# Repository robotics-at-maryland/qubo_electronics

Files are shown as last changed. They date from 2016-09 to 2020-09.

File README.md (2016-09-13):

# qubo_electronics

Welcome to the electronics repo for Project QUBO.
QUBO is an autonomous underwater vehicle and all of its electronics designs are stored here.

We use EAGLE for our circuit CAD.

eagleLibraries stores all the eagle libraries.

eagleDesigns sores all the boards that we design. Any design in this folder should ONLY USE COMPONENTS FROM THE eagleLibraries FOLDER.

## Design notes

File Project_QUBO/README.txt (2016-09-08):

This is the electronics folder for Project QUBO, the replacement for Tortuga 4.
===============================================================================

eagleLibraries is the EAGLE library folder.
	ALL robot PCB designs MUST only contain parts from libraries in the eagleLibraries directory.

datasheets is for all part datasheets used in the electronics designs.
	No subdirectories

eagleDesigns is for the actual eagle design files. 
	Subdirectories are created on a BOARD-BY-BOARD basis.
	If you're creating a new PCB, make a new folder. If you're editing an existing board, stay in the same folder.
	Use reason when creating new versions of files.

designDocumentation  is for design documentation.
	Use reason with file naming, no subdirectories.
	Document your design process ie. what your goal is, what options you considered, why you chose what you did, outline your final design selection, etc.
	Brownie points for LaTeX

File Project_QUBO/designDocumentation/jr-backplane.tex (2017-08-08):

\documentclass{article}

\usepackage{fancyhdr} % Required for custom headers
\usepackage{lastpage} % Required to determine the last page for the footer
\usepackage{extramarks} % Required for headers and footers
\usepackage[usenames,dvipsnames]{color} % Required for custom colors
\usepackage{graphicx} % Required to insert images
\usepackage{listings} % Required for insertion of code
\usepackage{courier} % Required for the courier font
\usepackage{amsfonts}
\usepackage{amsmath}
\usepackage{amssymb}
\usepackage{float}
\usepackage{siunitx}
\usepackage{hyperref}
\usepackage{wrapfig}

\graphicspath{ {Images/} }

%-------------------------------------------------------------------------------------------------
% DOCUMENT INFORMATION SPECIFIED HERE
%-------------------------------------------------------------------------------------------------
%% Assignment type, e.g. HW1, Project 2, Assignment 3
\newcommand{\assignmentType}{Interface Control Document}

%% Assignment title, e.g. Karger's Min Cut, Magnetic Fields
\newcommand{\assignmentTitle}{Qubo Electrical System}

%% Course number, e.g. ENEE324
\newcommand{\courseNum}{RoboSub 2017}

%% Course title, e.g. Advanced Signals and Systems
\newcommand{\courseTitle}{Submarine Hackathon}

%% Course professor
\newcommand{\prof}{RoboNation}

%% Department
\newcommand{\dept}{Department of Electrical and Computer Engineering}						

%% University
\newcommand{\univ}{University of Maryland}	

%% Seal image
\newcommand{\seal}{UMD_seal.png}					

%% Author
\newcommand{\student}{Ben Hurwitz}

% Margins
\topmargin=-0.45in
\evensidemargin=0in
\oddsidemargin=0in
\textwidth=6.5in
\textheight=9.0in
\headsep=0.25in

\linespread{0.9} % Line spacing

% Set up the header and footer
\pagestyle{fancy}
\rhead{\student} % Top left header
\lhead{\courseTitle : \assignmentType} % Top center head
%\rhead{\firstxmark} % Top right header
\lfoot{Last built:\ \today} % Bottom left footer
\cfoot{} % Bottom center footer
\rfoot{Page\ \thepage\ of\ \protect\pageref{LastPage}} % Bottom right footer
\renewcommand\headrulewidth{0.4pt} % Size of the header rule
\renewcommand\footrulewidth{0.4pt} % Size of the footer rule

\setlength\parindent{0pt} % Removes all indentation from paragraphs

\begin{document}

%----------------------------------------------------------------------------------------
%	TITLE PAGE
%----------------------------------------------------------------------------------------

\begin{titlepage}
    \begin{center}
        \vspace*{1cm}
        
        \Huge
        \textbf{\assignmentTitle}
        
        \vspace{0.5cm}
        \LARGE
        \assignmentType
        
        \vspace{1.5cm}
        
        \textbf{\student}
        
        \vfill
        
        \vspace{0.6cm}
        
        
        
        \vfill
        
        \Large
        \today	\\
        \courseNum : \courseTitle \\
        \prof \\
        \dept \\
        \univ \\
        
    \end{center}
\end{titlepage}

\tableofcontents
\listoffigures
\listoftables

\pagebreak

\section{Overview}
RoboSub 2017 came in a hurry, with little electrical working properly. The charging system lacked testing, the ORing chips had not demonstrated full capabilities, and the LT8640 5V/12V rail generators were completely unresponsive. This is to say that there was justification for the decision to scrap the charging and the LT8640s entirely for the far more reliable (and better known) PTN78020, the wide-range input 6A DC/DC buck converter made by TI that is controlled by a single resistor. It was a changed intended to make things simpler and improve robustness with known quantities. Instead, it pushed us (and by us, I mean me) towards to panic-region. In keeping with the Robotics At Maryland (RAM, or R@M) spirit, when we got to competition, none of the boards that were developed worked in any meaningful way, and thus we were forced to decide: spend time debugging, which was not something we are good at, or spend time further simplifying and hack it to get exactly the minimum of what was needed. By the end of day two, we had opted for the latter.
\paragraph{}
The resulting system was close to as barebones as could be, and by the time we actually went in and completed our qualifying run, the system was, in my opinion, the most minimalist system possible for our configuration. We had removed nearly all the sensors entirely, including the AHRS, depth, and internal temperature, choosing to rely simply on our mechanical stability and dead-reckoning to get us through. Thermal considerations were lost, or left to passive cooling options. The power control modules for the batteries were jettisoned for simple SPST switches and 30A fuses. Even the PCA9685 chips that we were using for PWM signalling were tossed aside. But in it's simplicity, Qubo worked for the first time, and qualification was achieved, so in this there was success where there had not been before. The system cuts out all the fat from previous iterations and reduces the entire electrical subsystem to a half dozen major components, including all voltage generation, that allowed Qubo to move forward.

\section{Details}
I have no images to show you at all, so if you'd like a more hands on view of the system, we should facetime or skype or whatever you kids use these days to go through it. The system runs off of a single battery, which was triggered by a simple SPST rocker switch to avoid the issues associated with plugging live power into other components. This 14.8V nominal goes through a single PTN, which is resistor-set (2.61kO) to output about 10V. (Why 10V? Because the PTN needs a 3V cushion to do it's converting, and a 12V output would require a minimum of 15V, not really feasible with this.) This 10V powers the Jetson (which takes down to 7V), and through the magnetic reed switch, triggers the main thruster relay. There are a number of capacitors on the input to the PTN - \textbf{DO NOT REMOVE THESE!!} Each of the ESCs on the output of the relay has a 220uF capacitor on it, which draws a large inrush current when voltage is applied. This causes significant voltage drop down to nearly 5V of the input source (batteries or shore), which kills the PTN, and thus kills the Jetson. The extra caps at the input of the PTN (notice how close they are) prevent this droop from being seen by the PTN, thus keeping it in operation. The ESCs themselves are mostly the same, except for the PWM signal generator. The PCA chip shorted, and we didn't have a backup, so we switched the embedded Arduino Uno to a TeensyDuino (TD), which has a dozen or so PWM outputs built-in. The TD is connected to the Jetson via a USB cable, which also power it. This gives us the ability to easily generate PWM signals directly from the embedded system. The only other thing is a single NCP1117 that converts the battery/shore voltage into 5V for the ethernet switch.
\paragraph{}
That, in essence, is the entire system. A single 10V rail powers the Jetson, which powers the embedded, and switches the thrusters on and off. Viola.

\section{Extras}
There are so many wires and so many parts that are still there but left unused or unconnected that it's hard to see this simplicity. The terminal block is used mostly to connect all the ESCs to the same high-voltage (V\_Batt) input, and to connect their outputs to the same ground. A second NCP1117 is left hanging and disconnected; it was used for some other bits that got summarily culled from the robot. There is a depth sensor which we believe (\textbf{but are not sure}) shorted at some point, thus rendering its data worthless. The AHRS works, but it's not reliable with all the changing currents within the pressure vessel. There are loose wires from two fans that were initially part of the vehicle as well - they are 3-wire black ribbon cables. The I2C line was removed entirely because of the removal of all associated devices, but the wires still remain. All the PWMs from the ESCs are bundled together into the TD; the signal and power grounds are tied together for simplicity; and the power and ground lines go right into the terminal block. 

\section{Moving Forward}
To be frank, the system looks like shit. It needs a good cleaning up. But I cannot emphasize enough that \textbf{it works}. Do not take this for granted! It is not easy to get all of this working, and tearing it down to make it look pretty will put a lot of pressure on you to build it back up again. It was tricky enough once. Use it as a platform to continue forward with, to build off of. Personally, I would use this next year to design small boards for each of the primary components (5V generator (PTN), 10V generator (PTN), TD), thoroughly test these, then combine them into a larger board with the necessary inputs and outputs. I would spend the first semester doing this; they're also smaller projects that can be given to new students without too much risk since they're all only a half dozen small components each at most. Make sure that the ESCs can more easily attach to the board! It should be a decent project for you. Pay close attention to how the wiring will be laid out! A major disappointment was not taking the wiring into enough consideration. It's a major size, weight, and obnoxious consideration. Take some time to think about how the wires should lay out, and discuss with Peter. Try to pull together mock-ups if you can, it'll help to visualize where things should be. 
\paragraph{}
If you get a nice single board that houses the single input, the 5V/10V generators, and the TD, and it has been tested thoroughly, then there are a number of small additional projects that can be developed. Add back in the depth sensor first. A single 5V I2C line \textbf{should} suffice, even though the Bar30 asks for a 3.3V I2C line (this has been bourne out in other testing, but you should verify! Collaborate with the software team on building a small jig to test this). The AHRS connects directly to the Jetson, so this is not a concern of yours, but something to keep in mind is shielding it from stray magnetic fields - use your PHYS271 and ENEE380/1 knowledge for this! (Moving charges generate magnetic fields.) Add some internal sensors - I'm thinking temperature in particular - using the same method: build a small component-specific board, test it completely, then integrate it into the larger board. Current and voltage sensors would also be nice, but those are something that a new EE can do without being critical to the system. 
\paragraph{}
My sense is that the critical parts on a single board can take a semester. For the second semester, focus on less critical, perhaps more long terms components. For this, you might consider integrating the DVL. We have the UWE isolated regulator already, and you can work through the noise reduction stuff while the other EEs develop the current sensor + fuse circuit we had previously for each of the thruster outputs. By next year's competition, you should be shooting for a very robust power system that is essentially a cleaner version of what I hacked together. Do not wait! Starting too late was a huge failure on my part. Get boards out to fab within a few weeks of starting, and continuously iterate. Note that for small boards, OshPark is fantastic (takes a bit longer, but only \$5 a square inch), while larger boards can be made with Advanced Circuit's \$33 deal. New EEs are developing breakout board for certain components. BUT the best thing you can do to make everyone's lives easier is to learn to use Design Blocks in Eagle. These will allow you to easily move a design from a smaller board to a larger one without any extra work. 
\paragraph{}
I won't tell you what to do, only suggest. But I believe it would be a colossal mistake to throw away the system as it is now to redesign again. Use what you have to test, and develop slowly. You have a nice foundation; don't throw it away because it looks like crap.
\par
Slack me if you have questions and I can try to help. Good luck with it - think of it as a bundle of small parts, and it becomes very doable.

\end{document}

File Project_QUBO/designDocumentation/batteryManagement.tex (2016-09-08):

\documentclass[12pt, letterpaper]{article}

\usepackage{amsmath}
\usepackage[margin=1in]{geometry}

\begin{document}
	\section{Design Goals}
		At a system level, the battery management subsystem lies between the batteries and the power supply/regulation system. The battery management system is responsible for balancing the batteries to create a single high voltage bus capable of powering all of the robot subsystems. It manages multiple battery cells (6 cells in Tortuga 4, 2 cells in Project QUBO). It must be capable of dealing with batteries of differing charge levels and therefore different voltages. Each battery is not capable of powering the entire robot so load balancing between the batteries, even with batteries of different voltages, is required. The battery management system is also responsible for providing a system to monitor the batteries and their containers. These monitoring systems include hot-plug detection, water sensors, and temperature sensors. Since Project QUBO contains two separate battery packs, hot-swapping support in the battery management system would also be desirable.
		
		\paragraph{General Goals}
		\begin{itemize}
			\item Balance 2 batteries and present a single battery-level rail to draw power from
			\item Provide a monitoring interface to ensure safe performance of the batteries
			\item Provide a method for connecting shore power to the robot
			\item Provide a method for turning battery power on/off
			\item Evaluate and possibly integrate hot-swapping functionality
		\end{itemize}
		
	\section{System Layout}
		
		Currently (March 2015), each of the 2 batteries will reside in their own hulls that are separate from the main electronics hull. This allows for easy battery removal from the system and for a smaller, simpler electronics hull. The battery management system is split between the electronics hull and battery hulls. Moreover, some of the battery management circuitry will reside on the same backplane PCB as the power regulation/distribution board. While this makes the power system more monolithic in nature, it will make systems integration on the robot much simpler since there will be only one power supply related board on the backplane.
		
		The battery management system will consist of two PCBs. One PCB will contain the balancing and hot-swapping circuitry and will be plugged into the backplane inside the main electronics hull. That PCB will be shared with the power regulation/distribution system. The other PCB will reside inside the battery hulls (so technically there will be 3 PCBs in the system since there are 2 battery hulls). The battery hull PCB will contain a mechanism to turn a battery on/off and provide monitoring circuitry to ensure the battery is functioning properly/safely inside the battery hulls.
		
	\section{Battery Balancing}
	
		In designing the battery balancing portion of the system, we found 2 possible methods for balancing the batteries to generate a single bus for the robot. We evaluated each method by taking efficiency, cost, and simplicity into account. 
		
		The first method is diode-ORing. This is the same method used the balance the 6 batteries (the main battery contained 5 27V batteries and the 6th 'cell' was the shore power) inside of Tortuga 4. 
\end{document}

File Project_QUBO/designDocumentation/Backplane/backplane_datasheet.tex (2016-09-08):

\documentclass{article}

\usepackage{fancyhdr} % Required for custom headers
\usepackage{lastpage} % Required to determine the last page for the footer
\usepackage{extramarks} % Required for headers and footers
\usepackage[usenames,dvipsnames]{color} % Required for custom colors
\usepackage{graphicx} % Required to insert images
\usepackage{listings} % Required for insertion of code
\usepackage{courier} % Required for the courier font
\usepackage{amsfonts}
\usepackage{amsmath}
\usepackage{amssymb}

%-------------------------------------------------------------------------------------------------
% DOCUMENT INFORMATION SPECIFIED HERE
%-------------------------------------------------------------------------------------------------
%% Assignment type, e.g. HW1, Project 2, Assignment 3
\newcommand{\assignmentType}{Technical Datasheet}

%% Assignment title, e.g. Karger's Min Cut, Magnetic Fields
\newcommand{\assignmentTitle}{Backplane}

%% Last edited date
\newcommand{\lastEdited}{8/2/16}

%% Course number, e.g. ENEE324
\newcommand{\courseNum}{}

%% Course title, e.g. Advanced Signals and Systems
\newcommand{\courseTitle}{Robotics@Maryland}

%% Course professor
\newcommand{\prof}{Institute for Systems Research}

%% Department
\newcommand{\dept}{Department of Electrical and Computer Engineering}						

%% University
\newcommand{\univ}{University of Maryland}	

%% Seal image
\newcommand{\seal}{C:/UMD_seal.png}					

%% Author
\newcommand{\student}{Ben Hurwitz}

% Margins
\topmargin=-0.45in
\evensidemargin=0in
\oddsidemargin=0in
\textwidth=6.5in
\textheight=9.0in
\headsep=0.25in

\linespread{0.9} % Line spacing

% Set up the header and footer
\pagestyle{fancy}
\rhead{\author} % Top left header
\lhead{\courseTitle : \assignmentType} % Top center head
%\rhead{\firstxmark} % Top right header
\lfoot{\lastxmark} % Bottom left footer
\cfoot{} % Bottom center footer
\rfoot{Page\ \thepage\ of\ \protect\pageref{LastPage}} % Bottom right footer
\renewcommand\headrulewidth{0.4pt} % Size of the header rule
\renewcommand\footrulewidth{0.4pt} % Size of the footer rule

\setlength\parindent{0pt} % Removes all indentation from paragraphs

\begin{document}

%----------------------------------------------------------------------------------------
%	TITLE PAGE
%----------------------------------------------------------------------------------------

\begin{titlepage}
    \begin{center}
        \vspace*{1cm}
        
        \Huge
        \textbf{\assignmentTitle}
        
        \vspace{0.5cm}
        \LARGE
        \assignmentType
        
        \vspace{1.5cm}
        
        \textbf{\student}
        
        \vfill
        
        \vspace{0.6cm}
        
        
        
        \vspace{1.5cm}
        
        \textbf{Last Edited: \lastEdited}
        
        \vfill
        
        \Large
        \courseTitle \\
        \prof \\
        \dept \\
        \univ \\
        
    \end{center}
\end{titlepage}

\tableofcontents

\section{Introduction}
The backplane is a four layer board that connects most of the electrical components together and passes signals between them. Physically, the board is approximately 20cm long and 10cm wide, sitting about 3.5 inches above the bottom of the electronics hulls, and consists of a 16V plane, a GND plane, and two internal signal planes. There are four major connectors for the fours plug-in daughterboards, which allow for flexibility and modularity, each with eighty signal pins and two full-power blades. There are two I$^2$C lines, two SPI lines, and two serial RX/TX lines that run between the CPU and all the daughterboards, as well as USB connections between the CPU and the individual daughterboards. 

\section{Connectors}
\subsection{Daughterboard Connection}
\subsection{CPU Connection}
\subsection{Hypertronics Connection}

\section{Signalling}
\subsection{USB}
\subsection{I$^2$C}
\subsection{SPI}
\subsection{Serial}

\section{Thrusters}

\section{Misc}
\subsection{Current Sensors}
\subsection{Debug port}
\subsection{Misc. Ports}

\section{Appendix}
\subsection{Current ratings}
\subsection{Thermal Considerations}
\subsection{Complete Parts List}

\end{document}

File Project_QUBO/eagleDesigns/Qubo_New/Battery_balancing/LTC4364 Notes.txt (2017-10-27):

LTC4364 Notes
	-M1 is normally fully on
	-When there is an overvoltage, the voltage amplifier controls the M1 gate and regulates
	 the voltage at the OUT pin set by the external resistive divider to ground and the internal 1.25 V reference
	-Overcurrent can be detected by the current sensing resistor between the SENSE and OUT pins
	-An IA (active current limit circuit) controls the gate of M1 to limit the sense voltage to 50mV if OUT is above 2.5V
	-During OV or OI event, a current source starts charging the TMR cap.  The pull-up current source in an OI event is 5 
	 times that of one in an OC event.  When TMR reaches 1.25V, FLT pulls low to warn impending turn off.  M1 stays on until
	 TMR reaches 1.35V, at which point HGATE pulls low and turns off M1. 
	-Fault timer period decreases with voltage across the MOSFET
	-If HGATE is latched low, briefly pulling SHDN below 0.5V resets the fault and lets HGATE pull high
	-The source and drain of MOSFET M2 act as the anode and cathode of the ideal diode
	-DGATE maintains a 30mV voltage across source and drain of M2.
	-If a reverse voltage exceeding -30mV flows across M2, DGATE pulls low and turns off M2
	-If VCC falls below GND voltage, DGATE is pulled to SOURCE pin voltage, keeping M2 off.  
	-If HGATE pulls low, DGATE also pulls low
	-If the output drops below GND, HGATE is pulled to SOURCE pin voltage, turning M1 off and shutting down the forward current
	 path
	-If UV detects an undervoltage, HGATE and DGATE remain low if UV is below its 1.25V threshold.  SHDN turns off both the
	 pass devices and internal circuitry, reducing supply current to 10uA.

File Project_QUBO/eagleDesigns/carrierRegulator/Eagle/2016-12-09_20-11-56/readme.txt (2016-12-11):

 

**********************************************************
*************  Important Instructions Follow  ************
**********************************************************
 
All files exported to: Z:\\48\\23\\4823925\\8\Eagle\2016-12-09_20-11-56\2016-12-09_20-11-56.xml

To import your new library into Eagle:
1. Start Eagle.
2. Select File -> New -> Library from the menu.
3. In the blank library window, select File -> Execute Script from the menu.
5. Browse to your newly exported Eagle Script file (".scr" file extension)
6. After opening the file, the script will populate the new library.
7. Use File -> Save (or Save As..) to save the library to the desired location in Eagle native format.

For additional information, please visit this site:
http://www.accelerated-designs.com/help/Eagle_import.html

You may also find this video helpful:
http://youtu.be/5jGuWY-Yy3Q

Component "GRM216R71H103KA01D" renamed to "GRM216R71H103KA01D"
Component "CC0805KRX7R9BB682" renamed to "CC0805KRX7R9BB682"
Component "CL21C271JBANFNC" renamed to "CL21C271JBANFNC"
Component "WB_CURRENT_LOAD" renamed to "WB_CURRENT_LOAD"
Component "C0805C104K5RACTU" renamed to "C0805C104K5RACTU"
Component "16SVPE180M" renamed to "16SVPE180M"
Component "CC0805KRX7R9BB681" renamed to "CC0805KRX7R9BB681"
Component "EMK212B7105KG-T" renamed to "EMK212B7105KG-T"
Component "B230A-13-F" renamed to "B230A-13-F"
Component "WB_GND" renamed to "WB_GND"
Component "PM2110-5R6M-RC" renamed to "PM2110-5R6M-RC"
Component "CSD17310Q5A" renamed to "CSD17310Q5A"
Component "CSD18537NQ5A" renamed to "CSD18537NQ5A"
Component "ERJ-6ENF8061V" renamed to "ERJ-6ENF8061V"
Component "ERJ-6ENF1004V" renamed to "ERJ-6ENF1004V"
Component "ERJ-6ENF1101V" renamed to "ERJ-6ENF1101V"
Component "ERJ-6ENF9761V" renamed to "ERJ-6ENF9761V"
Component "ERJ-6ENF4753V" renamed to "ERJ-6ENF4753V"
Component "CSNL1206FT3L00" renamed to "CSNL1206FT3L00"
Component "ERJ-6ENF1272V" renamed to "ERJ-6ENF1272V"
Component "ERJ-6ENF3161V" renamed to "ERJ-6ENF3161V"
Component "ERJ-6ENF2612V" renamed to "ERJ-6ENF2612V"
Component "LM25116MHX/NOPB" renamed to "LM25116MHX/NOPB"
Component "WB_BATTERY" renamed to "WB_BATTERY"
Component "GRM31CR71H475KA12L" renamed to "GRM31CR71H475KA12L"
The Symbol WB_CONTINUATION was missing a RefDes attribute, a refdes was created for the symbol.
The Symbol WB_CONTINUATION was missing a Type attribute, a type was created for the symbol.
The Symbol WB_CONTINUATION was missing a Value attribute, a value was created for the symbol.
The Symbol WB_CAP_OUTPUT was missing a RefDes attribute, a refdes was created for the symbol.
The Symbol WB_CAP_OUTPUT was missing a Type attribute, a type was created for the symbol.
The Symbol WB_CAP_OUTPUT was missing a Value attribute, a value was created for the symbol.
The Symbol WB_DIODE was missing a RefDes attribute, a refdes was created for the symbol.
The Symbol WB_DIODE was missing a Type attribute, a type was created for the symbol.
The Symbol WB_DIODE was missing a Value attribute, a value was created for the symbol.
The Symbol WB_CURRENT_PROBE was missing a RefDes attribute, a refdes was created for the symbol.
The Symbol WB_CURRENT_PROBE was missing a Type attribute, a type was created for the symbol.
The Symbol WB_CURRENT_PROBE was missing a Value attribute, a value was created for the symbol.
The Symbol WB_N_MOSFET was missing a RefDes attribute, a refdes was created for the symbol.
The Symbol WB_N_MOSFET was missing a Type attribute, a type was created for the symbol.
The Symbol WB_N_MOSFET was missing a Value attribute, a value was created for the symbol.
The Symbol WB_BLOCK_IO was missing a RefDes attribute, a refdes was created for the symbol.
The Symbol WB_BLOCK_IO was missing a Type attribute, a type was created for the symbol.
The Symbol WB_BLOCK_IO was missing a Value attribute, a value was created for the symbol.
The Symbol WB_LM25116 was missing a RefDes attribute, a refdes was created for the symbol.
The Symbol WB_LM25116 was missing a Type attribute, a type was created for the symbol.
The Symbol WB_LM25116 was missing a Value attribute, a value was created for the symbol.
The Symbol WB_VOLTAGE_PROBE was missing a RefDes attribute, a refdes was created for the symbol.
The Symbol WB_VOLTAGE_PROBE was missing a Type attribute, a type was created for the symbol.
The Symbol WB_VOLTAGE_PROBE was missing a Value attribute, a value was created for the symbol.
The Symbol WB_PWL_CURRENT_LOAD was missing a RefDes attribute, a refdes was created for the symbol.
The Symbol WB_PWL_CURRENT_LOAD was missing a Type attribute, a type was created for the symbol.
The Symbol WB_PWL_CURRENT_LOAD was missing a Value attribute, a value was created for the symbol.
The Symbol WB_PWL_VOLTAGE_SOURCE was missing a RefDes attribute, a refdes was created for the symbol.
The Symbol WB_PWL_VOLTAGE_SOURCE was missing a Type attribute, a type was created for the symbol.
The Symbol WB_PWL_VOLTAGE_SOURCE was missing a Value attribute, a value was created for the symbol.
The Symbol WB_SOURCE_RESISTOR was missing a RefDes attribute, a refdes was created for the symbol.
The Symbol WB_SOURCE_RESISTOR was missing a Type attribute, a type was created for the symbol.
The Symbol WB_SOURCE_RESISTOR was missing a Value attribute, a value was created for the symbol.
The Symbol WB_PRIM_PWL_VOLTAGE_SOURCE was missing a RefDes attribute, a refdes was created for the symbol.
The Symbol WB_PRIM_PWL_VOLTAGE_SOURCE was missing a Type attribute, a type was created for the symbol.
The Symbol WB_PRIM_PWL_VOLTAGE_SOURCE was missing a Value attribute, a value was created for the symbol.
The Symbol WB_PRIMITIVE_BATTERY was missing a RefDes attribute, a refdes was created for the symbol.
The Symbol WB_PRIMITIVE_BATTERY was missing a Type attribute, a type was created for the symbol.
The Symbol WB_PRIMITIVE_BATTERY was missing a Value attribute, a value was created for the symbol.
The Symbol WB_PRIM_AC_VOLTAGE_SOURCE was missing a RefDes attribute, a refdes was created for the symbol.
The Symbol WB_PRIM_AC_VOLTAGE_SOURCE was missing a Type attribute, a type was created for the symbol.
The Symbol WB_PRIM_AC_VOLTAGE_SOURCE was missing a Value attribute, a value was created for the symbol.
The Symbol WB_SYNC_CAPACITOR was missing a RefDes attribute, a refdes was created for the symbol.
The Symbol WB_SYNC_CAPACITOR was missing a Type attribute, a type was created for the symbol.
The Symbol WB_SYNC_CAPACITOR was missing a Value attribute, a value was created for the symbol.
The Symbol WB_PRIMITIVE_INDUCTOR was missing a RefDes attribute, a refdes was created for the symbol.
The Symbol WB_PRIMITIVE_INDUCTOR was missing a Type attribute, a type was created for the symbol.
The Symbol WB_PRIMITIVE_INDUCTOR was missing a Value attribute, a value was created for the symbol.
The Symbol WB_PRIM_STARTUP_VOLTAGE_SOURCE was missing a RefDes attribute, a refdes was created for the symbol.
The Symbol WB_PRIM_STARTUP_VOLTAGE_SOURCE was missing a Type attribute, a type was created for the symbol.
The Symbol WB_PRIM_STARTUP_VOLTAGE_SOURCE was missing a Value attribute, a value was created for the symbol.
The Symbol WB_STARTUP_VOLTAGE_SOURCE was missing a RefDes attribute, a refdes was created for the symbol.
The Symbol WB_STARTUP_VOLTAGE_SOURCE was missing a Type attribute, a type was created for the symbol.
The Symbol WB_STARTUP_VOLTAGE_SOURCE was missing a Value attribute, a value was created for the symbol.
The Symbol WB_LOAD_RESISTOR was missing a RefDes attribute, a refdes was created for the symbol.
The Symbol WB_LOAD_RESISTOR was missing a Type attribute, a type was created for the symbol.
The Symbol WB_LOAD_RESISTOR was missing a Value attribute, a value was created for the symbol.

Ultra Librarian Gold 8.1.204 Process Report

Message - Padstack "RX44Y57D0T" Shape(4) is a CIRCLE with no diameter.
Message - Padstack "RX44Y71D0T" Shape(4) is a CIRCLE with no diameter.
Message - Padstack "RX128Y32D0T" Shape(4) is a CIRCLE with no diameter.
Message - Padstack "RX86Y64D0T" Shape(4) is a CIRCLE with no diameter.
Message - Padstack "RX200Y700D0T" Shape(4) is a CIRCLE with no diameter.
Message - Padstack "RX31p5Y27p56D0T" Shape(4) is a CIRCLE with no diameter.
Message - Padstack "RX4p3Y4p56D0T" Shape(4) is a CIRCLE with no diameter.
Message - Padstack "RX56Y14D0T" Shape(4) is a CIRCLE with no diameter.
Message - Padstack "RX124Y171D0T" Shape(4) is a CIRCLE with no diameter.
Message - Component "GRM216R71H103KA01D" attribute "Cap" references text style "" that is not in the database.
The default pattern text style "H50s3" was substituted.
Message - Component "GRM216R71H103KA01D" attribute "ESR" references text style "" that is not in the database.
The default pattern text style "H50s3" was substituted.
Message - Component "GRM216R71H103KA01D" attribute "IRMS" references text style "" that is not in the database.
The default pattern text style "H50s3" was substituted.
Message - Component "GRM216R71H103KA01D" attribute "VDC" references text style "" that is not in the database.
The default pattern text style "H50s3" was substituted.
Message - Component "CC0805KRX7R9BB682" attribute "Cap" references text style "" that is not in the database.
The default pattern text style "H50s3" was substituted.
Message - Component "CC0805KRX7R9BB682" attribute "ESR" references text style "" that is not in the database.
The default pattern text style "H50s3" was substituted.
Message - Component "CC0805KRX7R9BB682" attribute "IRMS" references text style "" that is not in the database.
The default pattern text style "H50s3" was substituted.
Message - Component "CC0805KRX7R9BB682" attribute "VDC" references text style "" that is not in the database.
The default pattern text style "H50s3" was substituted.
Message - Component "CL21C271JBANFNC" attribute "Datasheet URL" references text style "" that is not in the database.
The default pattern text style "H50s3" was substituted.
Message - Component "CL21C271JBANFNC" attribute "Cap" references text style "" that is not in the database.
The default pattern text style "H50s3" was substituted.
Message - Component "CL21C271JBANFNC" attribute "ESR" references text style "" that is not in the database.
The default pattern text style "H50s3" was substituted.
Message - Component "CL21C271JBANFNC" attribute "IRMS" references text style "" that is not in the database.
The default pattern text style "H50s3" was substituted.
Message - Component "CL21C271JBANFNC" attribute "VDC" references text style "" that is not in the database.
The default pattern text style "H50s3" was substituted.
Message - Component "C0805C104K5RACTU" attribute "Cap" references text style "" that is not in the database.
The default pattern text style "H50s3" was substituted.
Message - Component "C0805C104K5RACTU" attribute "ESR" references text style "" that is not in the database.
The default pattern text style "H50s3" was substituted.
Message - Component "C0805C104K5RACTU" attribute "IRMS" references text style "" that is not in the database.
The default pattern text style "H50s3" was substituted.
Message - Component "C0805C104K5RACTU" attribute "VDC" references text style "" that is not in the database.
The default pattern text style "H50s3" was substituted.
Message - Component "16SVPE180M" attribute "Datasheet URL" references text style "" that is not in the database.
The default pattern text style "H50s3" was substituted.
Message - Component "16SVPE180M" attribute "Cap" references text style "" that is not in the database.
The default pattern text style "H50s3" was substituted.
Message - Component "16SVPE180M" attribute "ESR" references text style "" that is not in the database.
The default pattern text style "H50s3" was substituted.
Message - Component "16SVPE180M" attribute "IRMS" references text style "" that is not in the database.
The default pattern text style "H50s3" was substituted.
Message - Component "16SVPE180M" attribute "VDC" references text style "" that is not in the database.
The default pattern text style "H50s3" was substituted.
Message - Component "CC0805KRX7R9BB681" attribute "Cap" references text style "" that is not in the database.
The default pattern text style "H50s3" was substituted.
Message - Component "CC0805KRX7R9BB681" attribute "ESR" references text style "" that is not in the database.
The default pattern text style "H50s3" was substituted.
Message - Component "CC0805KRX7R9BB681" attribute "IRMS" references text style "" that is not in the database.
The default pattern text style "H50s3" was substituted.
Message - Component "CC0805KRX7R9BB681" attribute "VDC" references text style "" that is not in the database.
The default pattern text style "H50s3" was substituted.
Message - Component "EMK212B7105KG-T" attribute "Cap" references text style "" that is not in the database.
The default pattern text style "H50s3" was substituted.
Message - Component "EMK212B7105KG-T" attribute "ESR" references text style "" that is not in the database.
The default pattern text style "H50s3" was substituted.
Message - Component "EMK212B7105KG-T" attribute "IRMS" references text style "" that is not in the database.
The default pattern text style "H50s3" was substituted.
Message - Component "EMK212B7105KG-T" attribute "VDC" references text style "" that is not in the database.
The default pattern text style "H50s3" was substituted.
Message - Component "B230A-13-F" attribute "Datasheet URL" references text style "" that is not in the database.
The default pattern text style "H50s3" was substituted.
Message - Component "B230A-13-F" attribute "Io" references text style "" that is not in the database.
The default pattern text style "H50s3" was substituted.
Message - Component "B230A-13-F" attribute "VRRM" references text style "" that is not in the database.
The default pattern text style "H50s3" was substituted.
Message - Component "B230A-13-F" attribute "VFatIo" references text style "" that is not in the database.
The default pattern text style "H50s3" was substituted.
Message - Component "PM2110-5R6M-RC" attribute "L" references text style "" that is not in the database.
The default pattern text style "H50s3" was substituted.
Message - Component "PM2110-5R6M-RC" attribute "DCR" references text style "" that is not in the database.
The default pattern text style "H50s3" was substituted.
Message - Component "PM2110-5R6M-RC" attribute "IDC" references text style "" that is not in the database.
The default pattern text style "H50s3" was substituted.
Message - Component "CSD17310Q5A" attribute "Datasheet URL" references text style "" that is not in the database.
The default pattern text style "H50s3" was substituted.
Message - Component "CSD17310Q5A" attribute "VdsMax" references text style "" that is not in the database.
The default pattern text style "H50s3" was substituted.
Message - Component "CSD17310Q5A" attribute "IdsMax" references text style "" that is not in the database.
The default pattern text style "H50s3" was substituted.
Message - Component "CSD17310Q5A" attribute "Rdson45" references text style "" that is not in the database.
The default pattern text style "H50s3" was substituted.
Message - Component "CSD17310Q5A" attribute "QgTyp" references text style "" that is not in the database.
The default pattern text style "H50s3" was substituted.
Message - Component "CSD17310Q5A" attribute "Quantity" references text style "" that is not in the database.
The default pattern text style "H50s3" was substituted.
Message - Component "ERJ-6ENF8061V" attribute "Resistance" references text style "" that is not in the database.
The default pattern text style "H50s3" was substituted.
Message - Component "ERJ-6ENF8061V" attribute "Power" references text style "" that is not in the database.
The default pattern text style "H50s3" was substituted.
Message - Component "ERJ-6ENF8061V" attribute "Tolerance" references text style "" that is not in the database.
The default pattern text style "H50s3" was substituted.
Message - Component "ERJ-6ENF1004V" attribute "Resistance" references text style "" that is not in the database.
The default pattern text style "H50s3" was substituted.
Message - Component "ERJ-6ENF1004V" attribute "Power" references text style "" that is not in the database.
The default pattern text style "H50s3" was substituted.
Message - Component "ERJ-6ENF1004V" attribute "Tolerance" references text style "" that is not in the database.
The default pattern text style "H50s3" was substituted.
Message - Component "ERJ-6ENF1101V" attribute "Resistance" references text style "" that is not in the database.
The default pattern text style "H50s3" was substituted.
Message - Component "ERJ-6ENF1101V" attribute "Power" references text style "" that is not in the database.
The default pattern text style "H50s3" was substituted.
Message - Component "ERJ-6ENF1101V" attribute "Tolerance" references text style "" that is not in the database.
The default pattern text style "H50s3" was substituted.
Message - Component "ERJ-6ENF9761V" attribute "Resistance" references text style "" that is not in the database.
The default pattern text style "H50s3" was substituted.
Message - Component "ERJ-6ENF9761V" attribute "Power" references text style "" that is not in the database.
The default pattern text style "H50s3" was substituted.
Message - Component "ERJ-6ENF9761V" attribute "Tolerance" references text style "" that is not in the database.
The default pattern text style "H50s3" was substituted.
Message - Component "ERJ-6ENF4753V" attribute "Resistance" references text style "" that is not in the database.
The default pattern text style "H50s3" was substituted.
Message - Component "ERJ-6ENF4753V" attribute "Power" references text style "" that is not in the database.
The default pattern text style "H50s3" was substituted.
Message - Component "ERJ-6ENF4753V" attribute "Tolerance" references text style "" that is not in the database.
The default pattern text style "H50s3" was substituted.
Message - Component "CSNL1206FT3L00" attribute "Resistance" references text style "" that is not in the database.
The default pattern text style "H50s3" was substituted.
Message - Component "CSNL1206FT3L00" attribute "Power" references text style "" that is not in the database.
The default pattern text style "H50s3" was substituted.
Message - Component "CSNL1206FT3L00" attribute "Tolerance" references text style "" that is not in the database.
The default pattern text style "H50s3" was substituted.
Message - Component "ERJ-6ENF1272V" attribute "Resistance" references text style "" that is not in the database.
The default pattern text style "H50s3" was substituted.
Message - Component "ERJ-6ENF1272V" attribute "Power" references text style "" that is not in the database.
The default pattern text style "H50s3" was substituted.
Message - Component "ERJ-6ENF1272V" attribute "Tolerance" references text style "" that is not in the database.
The default pattern text style "H50s3" was substituted.
Message - Component "ERJ-6ENF3161V" attribute "Resistance" references text style "" that is not in the database.
The default pattern text style "H50s3" was substituted.
Message - Component "ERJ-6ENF3161V" attribute "Power" references text style "" that is not in the database.
The default pattern text style "H50s3" was substituted.
Message - Component "ERJ-6ENF3161V" attribute "Tolerance" references text style "" that is not in the database.
The default pattern text style "H50s3" was substituted.
Message - Component "ERJ-6ENF2612V" attribute "Resistance" references text style "" that is not in the database.
The default pattern text style "H50s3" was substituted.
Message - Component "ERJ-6ENF2612V" attribute "Power" references text style "" that is not in the database.
The default pattern text style "H50s3" was substituted.
Message - Component "ERJ-6ENF2612V" attribute "Tolerance" references text style "" that is not in the database.
The default pattern text style "H50s3" was substituted.
Message - Component "LM25116MHX/NOPB" attribute "Datasheet URL" references text style "" that is not in the database.
The default pattern text style "H50s3" was substituted.
Message - Component "LM25116MHX/NOPB" attribute "Frequency" references text style "" that is not in the database.
The default pattern text style "H50s3" was substituted.
Message - Component "LM25116MHX/NOPB" attribute "Imax" references text style "" that is not in the database.
The default pattern text style "H50s3" was substituted.
Message - Component "LM25116MHX/NOPB" attribute "Package" references text style "" that is not in the database.
The default pattern text style "H50s3" was substituted.
Message - Component "LM25116MHX/NOPB" attribute "Mktg_Package" references text style "" that is not in the database.
The default pattern text style "H50s3" was substituted.
Message - Component "LM25116MHX/NOPB" attribute "NSID" references text style "" that is not in the database.
The default pattern text style "H50s3" was substituted.
Message - Component "GRM31CR71H475KA12L" attribute "Cap" references text style "" that is not in the database.
The default pattern text style "H50s3" was substituted.
Message - Component "GRM31CR71H475KA12L" attribute "ESR" references text style "" that is not in the database.
The default pattern text style "H50s3" was substituted.
Message - Component "GRM31CR71H475KA12L" attribute "IRMS" references text style "" that is not in the database.
The default pattern text style "H50s3" was substituted.
Message - Component "GRM31CR71H475KA12L" attribute "VDC" references text style "" that is not in the database.
The default pattern text style "H50s3" was substituted.

TextStyle count:  24
Padstack count:   9
Pattern count:    7
Symbol count:     30
Component count:  25

Export

Footprint "WB_CURRENT_LOAD" has no layer data mapped and will be skipped.
Component "WB_CURRENT_LOAD" requires footprint "WB_CURRENT_LOAD" and will be skipped.
Footprint "WB_GND" has no layer data mapped and will be skipped.
Component "WB_GND" requires footprint "WB_GND" and will be skipped.
Footprint "WB_BATTERY" has no layer data mapped and will be skipped.
Component "WB_BATTERY" requires footprint "WB_BATTERY" and will be skipped.

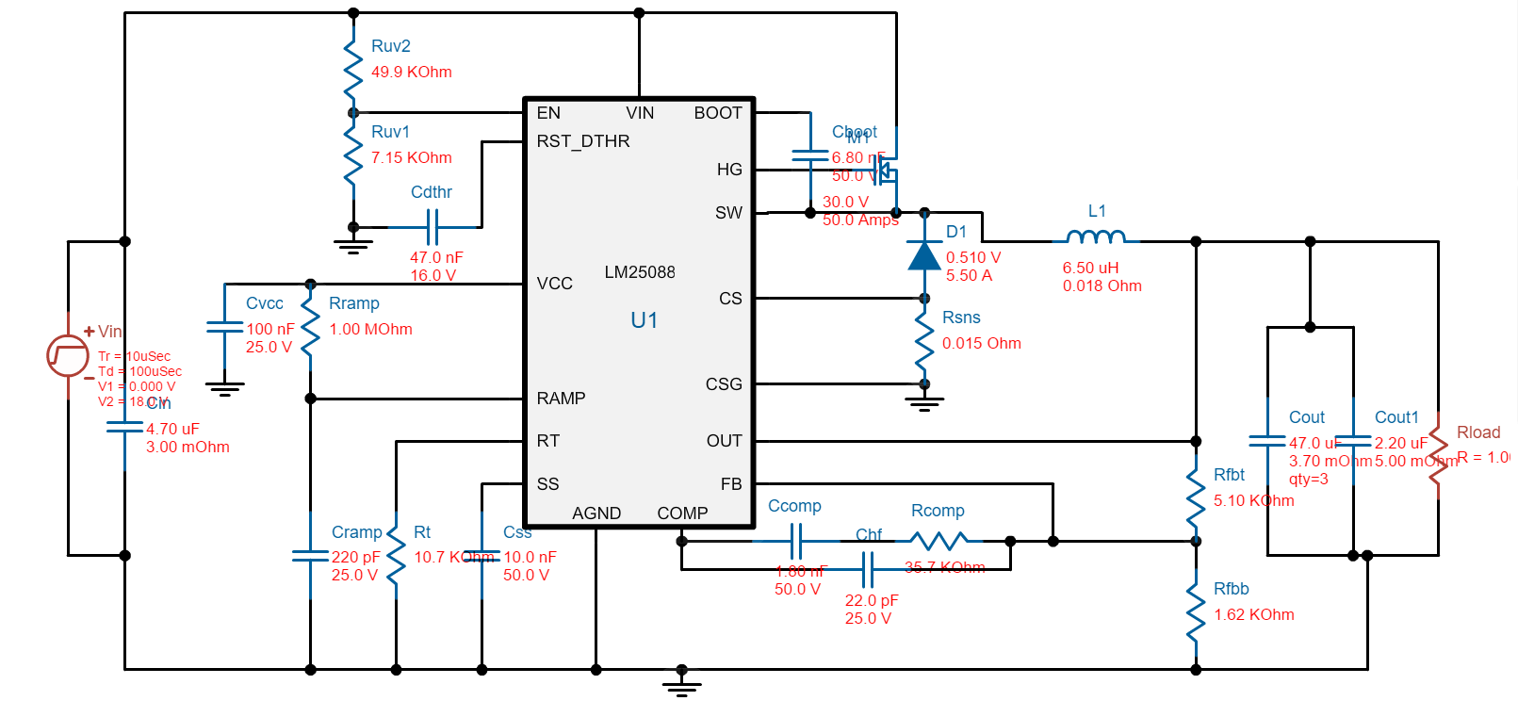
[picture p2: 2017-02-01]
Project_QUBO/eagleDesigns/carrierRegulator/lm5085.jpg

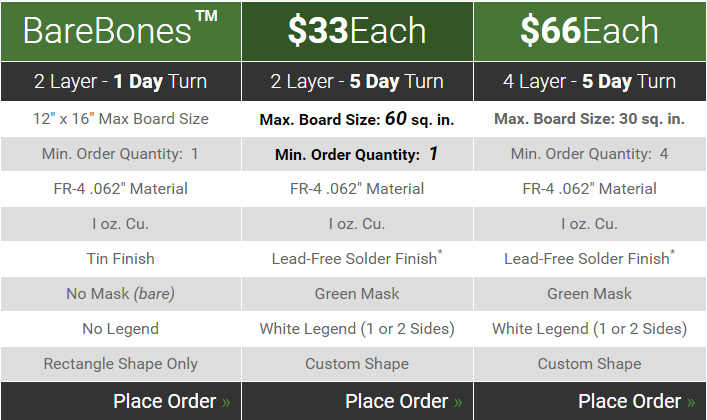
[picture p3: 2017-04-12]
Project_QUBO/4pcb-specs.PNG

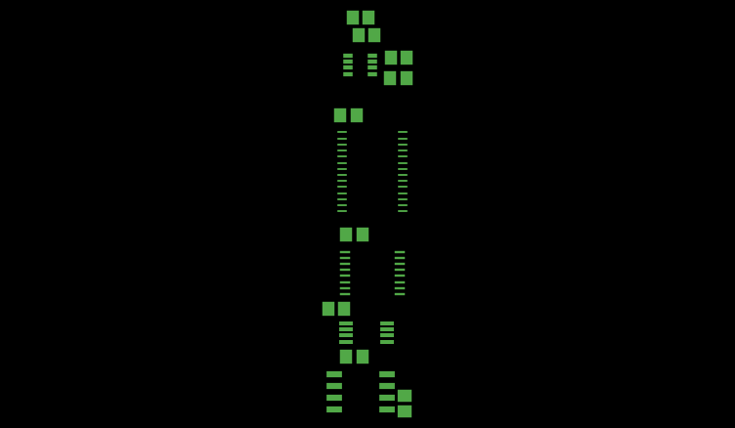
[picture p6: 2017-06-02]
Project_QUBO/eagleDesigns/Breadboards/gerbers/stencil.png

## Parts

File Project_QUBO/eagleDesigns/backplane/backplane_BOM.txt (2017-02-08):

Partlist exported from C:/Users/Ben/Documents/Dropbox/Documents/UMD/R@M/RAM Tran Electronics_2016/qubo_electronics.git/Project QUBO/eagleDesigns/backplane/version2/backplane_v4.sch at Tue, 2/7/2017 3:39 PM

Part             Value                     Device                    Package             Description                                                                               MF MPN     OC_FARNELL OC_NEWARK
2PIN_1           CPU_USB_HUB               KK254_VERT_2PIN22-29-2021 KK254_VERT_2PIN     KK® 254 Wire-to-Board Header, Vertical, with Friction Lock, 2 Circuits, Gold (Au) Plating                                
2PIN_2           CPU_USB_AHRS              KK254_VERT_2PIN22-29-2021 KK254_VERT_2PIN     KK® 254 Wire-to-Board Header, Vertical, with Friction Lock, 2 Circuits, Gold (Au) Plating                                
2PIN_3           CPU_USB_IMU               KK254_VERT_2PIN22-29-2021 KK254_VERT_2PIN     KK® 254 Wire-to-Board Header, Vertical, with Friction Lock, 2 Circuits, Gold (Au) Plating                                
2PIN_4           Magnetic Reed Switch plug KK254_VERT_2PIN22-29-2021 KK254_VERT_2PIN     KK® 254 Wire-to-Board Header, Vertical, with Friction Lock, 2 Circuits, Gold (Au) Plating                                
2PIN_5           CPU_USB_DVL               KK254_VERT_2PIN22-29-2021 KK254_VERT_2PIN     KK® 254 Wire-to-Board Header, Vertical, with Friction Lock, 2 Circuits, Gold (Au) Plating                                
2PIN_6           CPU_I2C_1                 KK254_VERT_2PIN22-29-2021 KK254_VERT_2PIN     KK® 254 Wire-to-Board Header, Vertical, with Friction Lock, 2 Circuits, Gold (Au) Plating                                
2PIN_7           CPU_CAN                   KK254_VERT_2PIN22-29-2021 KK254_VERT_2PIN     KK® 254 Wire-to-Board Header, Vertical, with Friction Lock, 2 Circuits, Gold (Au) Plating                                
4PIN_1           CPU_RS232_MCU             KK254_VERT_4PIN22-29-2041 KK254_VERT_4PIN     KK® 254 Wire-to-Board Header, Vertical, with Friction Lock, 4 Circuits, Gold (Au) Plating                                
4PIN_2           CPU_RS232_Flex            KK254_VERT_4PIN22-29-2041 KK254_VERT_4PIN     KK® 254 Wire-to-Board Header, Vertical, with Friction Lock, 4 Circuits, Gold (Au) Plating                                
4PIN_3           CPU_PWR1                  KK254_VERT_4PIN22-29-2041 KK254_VERT_4PIN     KK® 254 Wire-to-Board Header, Vertical, with Friction Lock, 4 Circuits, Gold (Au) Plating                                
4PIN_4           CPU_PWR2                  KK254_VERT_4PIN22-29-2041 KK254_VERT_4PIN     KK® 254 Wire-to-Board Header, Vertical, with Friction Lock, 4 Circuits, Gold (Au) Plating                                
4PIN_5           CPU_GND1                  KK254_VERT_4PIN22-29-2041 KK254_VERT_4PIN     KK® 254 Wire-to-Board Header, Vertical, with Friction Lock, 4 Circuits, Gold (Au) Plating                                
4PIN_6           CPU_GND2                  KK254_VERT_4PIN22-29-2041 KK254_VERT_4PIN     KK® 254 Wire-to-Board Header, Vertical, with Friction Lock, 4 Circuits, Gold (Au) Plating                                
4PIN_7           CPU_SPI                   KK254_VERT_4PIN22-29-2041 KK254_VERT_4PIN     KK® 254 Wire-to-Board Header, Vertical, with Friction Lock, 4 Circuits, Gold (Au) Plating                                
5.0              M250_5PIN                 M250_5PIN                 M205_5PIN           5-pin Eurostyle Terminal Block                                                                                           
5.1              M250_5PIN                 M250_5PIN                 M205_5PIN           5-pin Eurostyle Terminal Block                                                                                           
5.2              M250_5PIN                 M250_5PIN                 M205_5PIN           5-pin Eurostyle Terminal Block                                                                                           
5.3              M250_5PIN                 M250_5PIN                 M205_5PIN           5-pin Eurostyle Terminal Block                                                                                           
5.4              M250_5PIN                 M250_5PIN                 M205_5PIN           5-pin Eurostyle Terminal Block                                                                                           
5.5              M250_5PIN                 M250_5PIN                 M205_5PIN           5-pin Eurostyle Terminal Block                                                                                           
5.6              M250_5PIN                 M250_5PIN                 M205_5PIN           5-pin Eurostyle Terminal Block                                                                                           
5.7              M250_5PIN                 M250_5PIN                 M205_5PIN           5-pin Eurostyle Terminal Block                                                                                           
ACT-PWR_IN       SUPERSABRE_2CIRCUIT       SUPERSABRE_2CIRCUIT       SUPERSABRE_2CIRCUIT Molex SuperSabre                                                                                                         
ACT-PWR_OUT      SUPERSABRE_2CIRCUIT       SUPERSABRE_2CIRCUIT       SUPERSABRE_2CIRCUIT Molex SuperSabre                                                                                                         
BATTERY-MUX      PCA9546APW                PCA9546APW                TSSOP16             NXP 1:4 I2C Multiplexer                                                                                                  
C1               22p                       C-USC0805                 C0805               CAPACITOR, American symbol                                                                                               
C2               22p                       C-USC0805                 C0805               CAPACITOR, American symbol                                                                                               
C3               22p                       C-USC0805                 C0805               CAPACITOR, American symbol                                                                                               
C4               100n                      C-USC0805                 C0805               CAPACITOR, American symbol                                                                                               
C5               4.7u                      C-USC0805                 C0805               CAPACITOR, American symbol                                                                                               
C6               100n                      C-USC0805                 C0805               CAPACITOR, American symbol                                                                                               
C7               100n                      C-USC0805                 C0805               CAPACITOR, American symbol                                                                                               
C8               100n                      C-USC0805                 C0805               CAPACITOR, American symbol                                                                                               
C9               4.7u                      C-USC0805                 C0805               CAPACITOR, American symbol                                                                                               
C10              100n                      C-USC0805                 C0805               CAPACITOR, American symbol                                                                                               
C11              100n                      C-USC0805                 C0805               CAPACITOR, American symbol                                                                                               
C16              0.1u                      C-USC0805                 C0805               CAPACITOR, American symbol                                                                                               
C17              0.1u                      C-USC0805                 C0805               CAPACITOR, American symbol                                                                                               
C18              0.1u                      C-USC0805                 C0805               CAPACITOR, American symbol                                                                                               
C19              0.1u                      C-USC0805                 C0805               CAPACITOR, American symbol                                                                                               
C20              0.1u                      C-USC0805                 C0805               CAPACITOR, American symbol                                                                                               
C26              0.1u                      C-USC0805                 C0805               CAPACITOR, American symbol                                                                                               
C27              0.1u                      C-USC0805                 C0805               CAPACITOR, American symbol                                                                                               
C28              4.7u                      C-USC0805                 C0805               CAPACITOR, American symbol                                                                                               
C29              0.1u                      C-USC0805                 C0805               CAPACITOR, American symbol                                                                                               
C30              22p                       C-USC0805                 C0805               CAPACITOR, American symbol                                                                                               
C31              22p                       C-USC0805                 C0805               CAPACITOR, American symbol                                                                                               
C32              22p                       C-USC0805                 C0805               CAPACITOR, American symbol                                                                                               
C33              22p                       C-USC0805                 C0805               CAPACITOR, American symbol                                                                                               
C34              22p                       C-USC0805                 C0805               CAPACITOR, American symbol                                                                                               
C35              22p                       C-USC0805                 C0805               CAPACITOR, American symbol                                                                                               
C36              22p                       C-USC0805                 C0805               CAPACITOR, American symbol                                                                                               
C37              22p                       C-USC0805                 C0805               CAPACITOR, American symbol                                                                                               
C38              22p                       C-USC0805                 C0805               CAPACITOR, American symbol                                                                                               
C39              22p                       C-USC0805                 C0805               CAPACITOR, American symbol                                                                                               
C40              22p                       C-USC0805                 C0805               CAPACITOR, American symbol                                                                                               
C41              22p                       C-USC0805                 C0805               CAPACITOR, American symbol                                                                                               
C42              22p                       C-USC0805                 C0805               CAPACITOR, American symbol                                                                                               
C43              22p                       C-USC0805                 C0805               CAPACITOR, American symbol                                                                                               
C44              22p                       C-USC0805                 C0805               CAPACITOR, American symbol                                                                                               
C45              22p                       C-USC0805                 C0805               CAPACITOR, American symbol                                                                                               
C46              22p                       C-USC0805                 C0805               CAPACITOR, American symbol                                                                                               
C47              22p                       C-USC0805                 C0805               CAPACITOR, American symbol                                                                                               
C48              22p                       C-USC0805                 C0805               CAPACITOR, American symbol                                                                                               
D1               14V                       ZENER-DIODESOD123         SOD123              Z-Diode                                                                                                                  
D2               5V                        ZENER-DIODESOD123         SOD123              Z-Diode                                                                                                                  
D3               5V                        ZENER-DIODESOD123         SOD123              Z-Diode                                                                                                                  
D4               12V                       ZENER-DIODESOD123         SOD123              Z-Diode                                                                                                                  
D5               12V                       ZENER-DIODESOD123         SOD123              Z-Diode                                                                                                                  
D6               12V                       ZENER-DIODESOD123         SOD123              Z-Diode                                                                                                                  
D7               12V                       ZENER-DIODESOD123         SOD123              Z-Diode                                                                                                                  
D8               V_BATT                    ZENER-DIODESOD123         SOD123              Z-Diode                                                                                                                  
D9               V_BATT                    ZENER-DIODESOD123         SOD123              Z-Diode                                                                                                                  
D10              5V                        ZENER-DIODESOD123         SOD123              Z-Diode                                                                                                                  
D11              12V                       ZENER-DIODESOD123         SOD123              Z-Diode                                                                                                                  
D12              5V                        ZENER-DIODESOD123         SOD123              Z-Diode                                                                                                                  
D13              3V3                       ZENER-DIODESOD123         SOD123              Z-Diode                                                                                                                  
D14              V_BATT                    ZENER-DIODESOD123         SOD123              Z-Diode                                                                                                                  
D15              12V                       ZENER-DIODESOD123         SOD123              Z-Diode                                                                                                                  
D16              5V                        ZENER-DIODESOD123         SOD123              Z-Diode                                                                                                                  
D17              3V3                       ZENER-DIODESOD123         SOD123              Z-Diode                                                                                                                  
D18              V_BATT                    ZENER-DIODESOD123         SOD123              Z-Diode                                                                                                                  
D19              12V                       ZENER-DIODESOD123         SOD123              Z-Diode                                                                                                                  
D20              5V                        ZENER-DIODESOD123         SOD123              Z-Diode                                                                                                                  
D21              3V3                       ZENER-DIODESOD123         SOD123              Z-Diode                                                                                                                  
D22              V_BATT                    ZENER-DIODESOD123         SOD123              Z-Diode                                                                                                                  
D23              12V                       ZENER-DIODESOD123         SOD123              Z-Diode                                                                                                                  
D24              5V                        ZENER-DIODESOD123         SOD123              Z-Diode                                                                                                                  
D25              3V3                       ZENER-DIODESOD123         SOD123              Z-Diode                                                                                                                  
D26              V_BATT                    ZENER-DIODESOD123         SOD123              Z-Diode                                                                                                                  
D27              12V                       ZENER-DIODESOD123         SOD123              Z-Diode                                                                                                                  
D28              V_BATT                    ZENER-DIODESOD123         SOD123              Z-Diode                                                                                                                  
D29              V_BATT                    ZENER-DIODESOD123         SOD123              Z-Diode                                                                                                                  
D30              V_BATT                    ZENER-DIODESOD123         SOD123              Z-Diode                                                                                                                  
D31              V_BATT                    ZENER-DIODESOD123         SOD123              Z-Diode                                                                                                                  
D32              V_BATT                    ZENER-DIODESOD123         SOD123              Z-Diode                                                                                                                  
D33              V_BATT                    ZENER-DIODESOD123         SOD123              Z-Diode                                                                                                                  
D34              V_BATT                    ZENER-DIODESOD123         SOD123              Z-Diode                                                                                                                  
D35              V_BATT                    ZENER-DIODESOD123         SOD123              Z-Diode                                                                                                                  
D36              5V                        ZENER-DIODESOD123         SOD123              Z-Diode                                                                                                                  
D37              5V                        ZENER-DIODESOD123         SOD123              Z-Diode                                                                                                                  
D39              5V                        ZENER-DIODESOD123         SOD123              Z-Diode                                                                                                                  
D40              5V                        ZENER-DIODESOD123         SOD123              Z-Diode                                                                                                                  
D41              5V                        ZENER-DIODESOD123         SOD123              Z-Diode                                                                                                                  
DVL_HOST_FTDI    FT232RQ                   FT232RQ                   QFN32               Source: http://www.ftdichip.com/Documents/DataSheets/DS_FT232R_v104.pdf                      FT232RQ 1146033    91K9919  
DVL_SLAVE_FTDI   FT232RQ                   FT232RQ                   QFN32               Source: http://www.ftdichip.com/Documents/DataSheets/DS_FT232R_v104.pdf                      FT232RQ 1146033    91K9919  
DVL_TTL-TO-RS232 MAX213CDBR                MAX213CDBR                SSOP28DB            Texas Instruments MAX213CDBR                                                                                             
DVL_USB_HUB      USB2412-DZK               USB2412-DZK               QFN-28              SMSC USB2412                                                                                                             
G1                                         TPS2044BBD-SOIC           TPS2044             Texas Instruments TPS2044BD-SOIC                                                                                         
JP1              MPTC-01-80                MPTC-01-80                MPTC-01-80          Samtec 30A Signal/Power Combo System                                                                                     
JP2              MPTC-01-80                MPTC-01-80                MPTC-01-80          Samtec 30A Signal/Power Combo System                                                                                     
JP3              MPTC-01-80                MPTC-01-80                MPTC-01-80          Samtec 30A Signal/Power Combo System                                                                                     
JP4              MPTC-01-80                MPTC-01-80                MPTC-01-80          Samtec 30A Signal/Power Combo System                                                                                     
LED1             Red                       LEDCHIPLED_0805           CHIPLED_0805        LED                                                                                                                      
LED2             Green                     LEDCHIPLED_0805           CHIPLED_0805        LED                                                                                                                      
LED3             Red                       LEDCHIPLED_0805           CHIPLED_0805        LED                                                                                                                      
LED4             Green                     LEDCHIPLED_0805           CHIPLED_0805        LED                                                                                                                      
LED7             Green                     LEDCHIPLED_0805           CHIPLED_0805        LED                                                                                                                      
LED8             Green                     LEDCHIP-LED0805           CHIP-LED0805        LED                                                                                                                      
LED9             Red                       LEDCHIP-LED0805           CHIP-LED0805        LED                                                                                                                      
LED10            Red                       LEDCHIP-LED0805           CHIP-LED0805        LED                                                                                                                      
LED11            Green                     LEDCHIP-LED0805           CHIP-LED0805        LED                                                                                                                      
LED12            Red                       LEDCHIP-LED0805           CHIP-LED0805        LED                                                                                                                      
LED13            Green                     LEDCHIP-LED0805           CHIP-LED0805        LED                                                                                                                      
LED14            Red                       LEDCHIP-LED0805           CHIP-LED0805        LED                                                                                                                      
LED15            Green                     LEDCHIP-LED0805           CHIP-LED0805        LED                                                                                                                      
R1               200k                      R-US_R0805                R0805               RESISTOR, American symbol                                                                                                
R2               15k                       R-US_R0805                R0805               RESISTOR, American symbol                                                                                                
R3               27                        R-US_R0805                R0805               RESISTOR, American symbol                                                                                                
R4               270                       R-US_R0805                R0805               RESISTOR, American symbol                                                                                                
R5               270                       R-US_R0805                R0805               RESISTOR, American symbol                                                                                                
R6               270                       R-US_R0805                R0805               RESISTOR, American symbol                                                                                                
R7               270                       R-US_R0805                R0805               RESISTOR, American symbol                                                                                                
R8               5k                        R-US_R0805                R0805               RESISTOR, American symbol                                                                                                
R9               5k                        R-US_R0805                R0805               RESISTOR, American symbol                                                                                                
R10              50k                       R-US_R0805                R0805               RESISTOR, American symbol                                                                                                
R11              50k                       R-US_R0805                R0805               RESISTOR, American symbol                                                                                                
R12              12k+/-1%                  R-US_R0805                R0805               RESISTOR, American symbol                                                                                                
R13              100>R>40                  R-US_R0805                R0805               RESISTOR, American symbol                                                                                                
R14              50k                       R-US_R0805                R0805               RESISTOR, American symbol
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

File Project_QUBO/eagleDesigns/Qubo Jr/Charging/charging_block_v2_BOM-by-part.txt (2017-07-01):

Partlist exported from C:/Users/Ben/Documents/Dropbox/UMD/R@M/RAM Tran Electronics_2016/qubo_electronics.git/Project QUBO/eagleDesigns/Jr Support/Charging/charging_block_v2.sch at Wed, 6/14/2017 12:29 PM

Part            Value                     Device                    Package             Description                                                                               
5-TVS_1         BZA408B                   BZA408B                   SOT457              Nexperia BZA408B                                                                          
24V-TVS_1       VTVS                      VTVS                      DO-219AB            Vishay VTVS5V0ASMF to VTVS63GSMF                                                          
24V-TVS_2       VTVS                      VTVS                      DO-219AB            Vishay VTVS5V0ASMF to VTVS63GSMF                                                          
24V-TVS_OUT     VTVS                      VTVS                      DO-219AB            Vishay VTVS5V0ASMF to VTVS63GSMF                                                          
B1-ZENER                                  SCHOTTKY-DIODESOD-106     SOD106-R            Schottky Diode                                                                            
BATT1_FUSE      4A                        154-OMNI_BLOK             154-OMNI-BLOK       Littelfuse NANO2 Series 154 Omni-Blok fuseholder                                          
BATT1_IC        MAX1737                   MAX1737                   QSOP28              Maxim MAX1737 Stand-Alone Switch-Mode Lithium-Ion Battery-Charger Controller              
BATT1_IN        2_SUPERSABRE              2_SUPERSABRE              SUPERSABRE_2CIRCUIT Molex SuperSabre                                                                          
BATT1_SWITCH    GPTS203212B               GPTS203212B               GPTS203211B         CW Industries Pushbutton SPST switch                                                      
BUZZER          KK254_VERT_2PIN22-29-2021 KK254_VERT_2PIN22-29-2021 KK254_VERT_2PIN     KK® 254 Wire-to-Board Header, Vertical, with Friction Lock, 2 Circuits, Gold (Au) Plating 
C11             2.2u                      C-USC0805                 C0805               CAPACITOR, American symbol                                                                
C20             2.2u                      C-USC0805                 C0805               CAPACITOR, American symbol                                                                
C60             1u                        C-USC0805                 C0805               CAPACITOR, American symbol                                                                
C61             10u                       C-USC0805                 C0805               CAPACITOR, American symbol                                                                
C62             10u                       C-USC0805                 C0805               CAPACITOR, American symbol                                                                
C63             0.1u                      C-USC0805                 C0805               CAPACITOR, American symbol                                                                
C66             2.2u                      C-USC0805                 C0805               CAPACITOR, American symbol                                                                
C67             2.2u                      C-USC0805                 C0805               CAPACITOR, American symbol                                                                
C69             1u                        C-USC0805                 C0805               CAPACITOR, American symbol                                                                
C70             0.1u                      C-USC0805                 C0805               CAPACITOR, American symbol                                                                
C71             1n                        C-USC0805                 C0805               CAPACITOR, American symbol                                                                
C72             47n                       C-USC0805                 C0805               CAPACITOR, American symbol                                                                
C73             47n                       C-USC0805                 C0805               CAPACITOR, American symbol                                                                
C74             1n                        C-USC0805                 C0805               CAPACITOR, American symbol                                                                
C75             1n                        C-USC0805                 C0805               CAPACITOR, American symbol                                                                
C78             0.1u                      C-USC0805                 C0805               CAPACITOR, American symbol                                                                
C79             0.1u                      C-USC0805                 C0805               CAPACITOR, American symbol                                                                
C82             0.1u                      C-USC0805                 C0805               CAPACITOR, American symbol                                                                
C83             0.1u                      C-USC0805                 C0805               CAPACITOR, American symbol                                                                
C84             120u                      CPOL-USE3.5-8             E3,5-8              POLARIZED CAPACITOR, American symbol                                                      
CHARGING-SWITCH KK254_VERT_2PIN22-29-2021 KK254_VERT_2PIN22-29-2021 KK254_VERT_2PIN     KK® 254 Wire-to-Board Header, Vertical, with Friction Lock, 2 Circuits, Gold (Au) Plating 
D1                                        DIODE-SOD123              SOD123              DIODE                                                                                     
INPUT-SWITCH    GPTS203212B               GPTS203212B               GPTS203211B         CW Industries Pushbutton SPST switch                                                      
L1              10uH                      L-USL6100                 L6100               INDUCTOR, American symbol                                                                 
LED1            FASTCHG                   LEDCHIP-LED0805           CHIP-LED0805        LED                                                                                       
LED2            FULLCHG                   LEDCHIP-LED0805           CHIP-LED0805        LED                                                                                       
LED3            FAULT                     LEDCHIP-LED0805           CHIP-LED0805        LED                                                                                       
LED4            Batt Connect.             LEDCHIP-LED0805           CHIP-LED0805        LED                                                                                       
LED7            Shore Power               LEDCHIP-LED0805           CHIP-LED0805        LED                                                                                       
LED8            CHARGING                  LEDCHIP-LED0805           CHIP-LED0805        LED                                                                                       
NMOS1           STD95N2LH5                STD95N2LH5                DPAK                ST STD95N2LH5                                                                             
NMOS2           STD95N2LH5                STD95N2LH5                DPAK                ST STD95N2LH5                                                                             
NMOS3           IPD50P04P4-13             IPD50P04P4-13             TO252-3             Infineon IPD50P04P4-13                                                                    
NMOS4           IPD50P04P4-13             IPD50P04P4-13             TO252-3             Infineon IPD50P04P4-13                                                                    
R1              2.1k                      R-US_R0805                R0805               RESISTOR, American symbol                                                                 
R4              43k                       R-US_R0805                R0805               RESISTOR, American symbol                                                                 
R6              4.3k                      R-US_R0805                R0805               RESISTOR, American symbol                                                                 
R9              1.2k                      R-US_R0805                R0805               RESISTOR, American symbol                                                                 
R10             50k                       R-US_R0805                R0805               RESISTOR, American symbol                                                                 
R11             1.2k                      R-US_R0805                R0805               RESISTOR, American symbol                                                                 
R12             50k                       R-US_R0805                R0805               RESISTOR, American symbol                                                                 
R13             510                       R-US_R0805                R0805               RESISTOR, American symbol                                                                 
R14             50k                       R-US_R0805                R0805               RESISTOR, American symbol                                                                 
R19             680                       R-US_R0805                R0805               RESISTOR, American symbol                                                                 
R23             510                       R-US_R0805                R0805               RESISTOR, American symbol                                                                 
R24             6.8k                      R-US_R0805                R0805               RESISTOR, American symbol                                                                 
R25             43k                       R-US_R0805                R0805               RESISTOR, American symbol                                                                 
R26             4.3k                      R-US_R0805                R0805               RESISTOR, American symbol                                                                 
R28             1.5k                      R-US_R0805                R0805               RESISTOR, American symbol                                                                 
R29             100m                      R-US_R2512                R2512               RESISTOR, American symbol                                                                 
R30             50k                       R-US_R0805                R0805               RESISTOR, American symbol                                                                 
R31             50k                       R-US_R0805                R0805               RESISTOR, American symbol                                                                 
R32             10k                       R-US_R0805                R0805               RESISTOR, American symbol                                                                 
R33             330                       R-US_R0805                R0805               RESISTOR, American symbol                                                                 
R34             100m                      R-US_R2512                R2512               RESISTOR, American symbol                                                                 
SHORE_IN        2_SUPERSABRE              2_SUPERSABRE              SUPERSABRE_2CIRCUIT Molex SuperSabre                                                                          
SHORE_OUT       2_SUPERSABRE              2_SUPERSABRE              SUPERSABRE_2CIRCUIT Molex SuperSabre                                                                          
THERM           NTCLE201E3                NTCLE201E3                2-0.3MM-LEADS       Vishay NTC Thermistor                                                                     
U7              SSM3J353F                 SSM3J353F                 SOT-346-3/S-MINI    Toshiba SSM3J353F                                                                         
U8              SSM3J353F                 SSM3J353F                 SOT-346-3/S-MINI    Toshiba SSM3J353F                                                                         
U9              SSM3J353F                 SSM3J353F                 SOT-346-3/S-MINI    Toshiba SSM3J353F                                                                         
U56             74LVC1G14                 74LVC1G14                 TSSOP5              Nexperia 74LVC1G14                                                                        
U57             NCP1117                   NCP1117                   SOT-223             ON Semiconductor NCP1117

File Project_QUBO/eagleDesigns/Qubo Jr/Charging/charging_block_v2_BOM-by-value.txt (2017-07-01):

Partlist exported from C:/Users/Ben/Documents/Dropbox/UMD/R@M/RAM Tran Electronics_2016/qubo_electronics.git/Project QUBO/eagleDesigns/Jr Support/Charging/charging_block_v2.sch at Wed, 6/14/2017 12:29 PM

Qty Value                     Device                    Package             Parts                             Description                                                                               
1                             DIODE-SOD123              SOD123              D1                                DIODE                                                                                     
1                             SCHOTTKY-DIODESOD-106     SOD106-R            B1-ZENER                          Schottky Diode                                                                            
6   0.1u                      C-USC0805                 C0805               C63, C70, C78, C79, C82, C83      CAPACITOR, American symbol                                                                
2   1.2k                      R-US_R0805                R0805               R9, R11                           RESISTOR, American symbol                                                                 
1   1.5k                      R-US_R0805                R0805               R28                               RESISTOR, American symbol                                                                 
2   100m                      R-US_R2512                R2512               R29, R34                          RESISTOR, American symbol                                                                 
1   10k                       R-US_R0805                R0805               R32                               RESISTOR, American symbol                                                                 
2   10u                       C-USC0805                 C0805               C61, C62                          CAPACITOR, American symbol                                                                
1   10uH                      L-USL6100                 L6100               L1                                INDUCTOR, American symbol                                                                 
1   120u                      CPOL-USE3.5-8             E3,5-8              C84                               POLARIZED CAPACITOR, American symbol                                                      
3   1n                        C-USC0805                 C0805               C71, C74, C75                     CAPACITOR, American symbol                                                                
2   1u                        C-USC0805                 C0805               C60, C69                          CAPACITOR, American symbol                                                                
1   2.1k                      R-US_R0805                R0805               R1                                RESISTOR, American symbol                                                                 
4   2.2u                      C-USC0805                 C0805               C11, C20, C66, C67                CAPACITOR, American symbol                                                                
3   2_SUPERSABRE              2_SUPERSABRE              SUPERSABRE_2CIRCUIT BATT1_IN, SHORE_IN, SHORE_OUT     Molex SuperSabre                                                                          
1   330                       R-US_R0805                R0805               R33                               RESISTOR, American symbol                                                                 
2   4.3k                      R-US_R0805                R0805               R6, R26                           RESISTOR, American symbol                                                                 
2   43k                       R-US_R0805                R0805               R4, R25                           RESISTOR, American symbol                                                                 
2   47n                       C-USC0805                 C0805               C72, C73                          CAPACITOR, American symbol                                                                
1   4A                        154-OMNI_BLOK             154-OMNI-BLOK       BATT1_FUSE                        Littelfuse NANO2 Series 154 Omni-Blok fuseholder                                          
5   50k                       R-US_R0805                R0805               R10, R12, R14, R30, R31           RESISTOR, American symbol
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

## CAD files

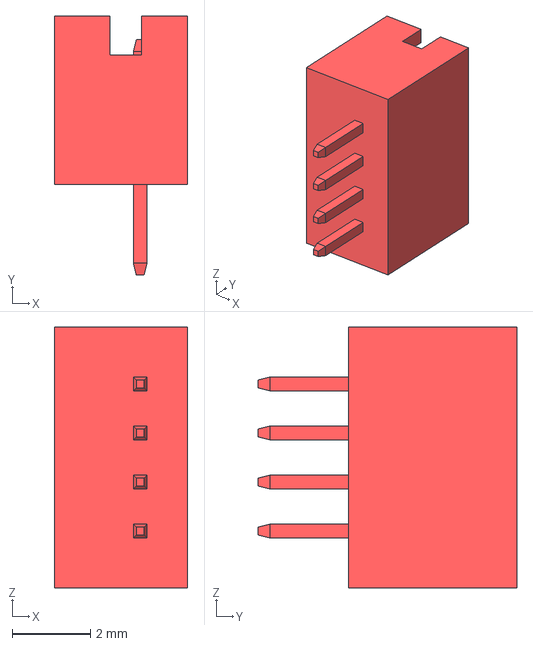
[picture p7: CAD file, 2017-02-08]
Project_QUBO/cadFiles/Backplane/DF13-4P-1.25DSA.igs
3.40 x 6.60 x 6.65 mm

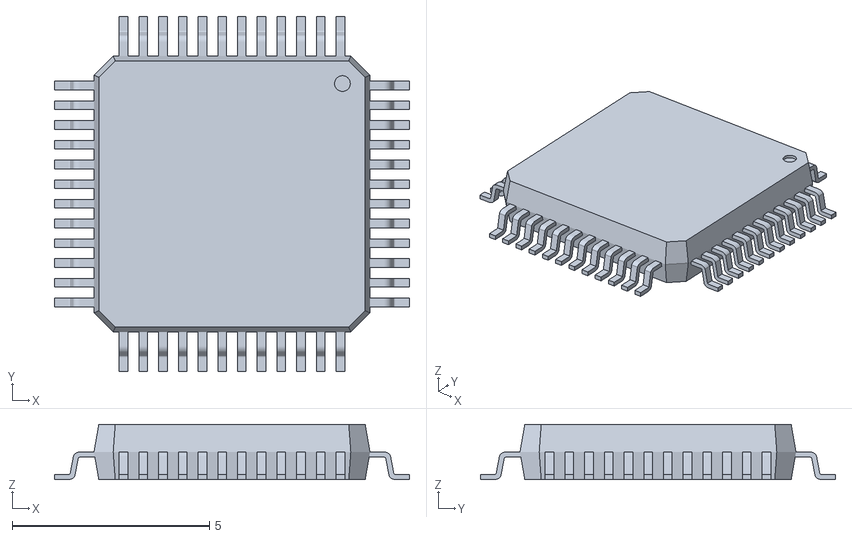
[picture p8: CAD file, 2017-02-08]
Project_QUBO/cadFiles/Backplane/LQFP_package/AB2_LQFP48_WINGS3D.stl
9.00 x 9.00 x 1.40

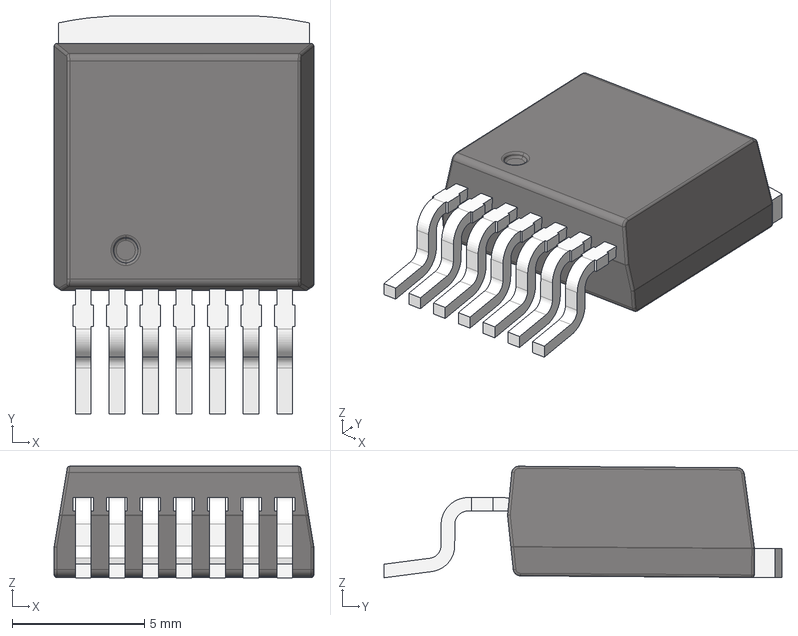
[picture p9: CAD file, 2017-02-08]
Project_QUBO/cadFiles/Backplane/PG-TO263-7-3/TO263-7-1.stp
9.82 x 15.1 x 4.22 mm

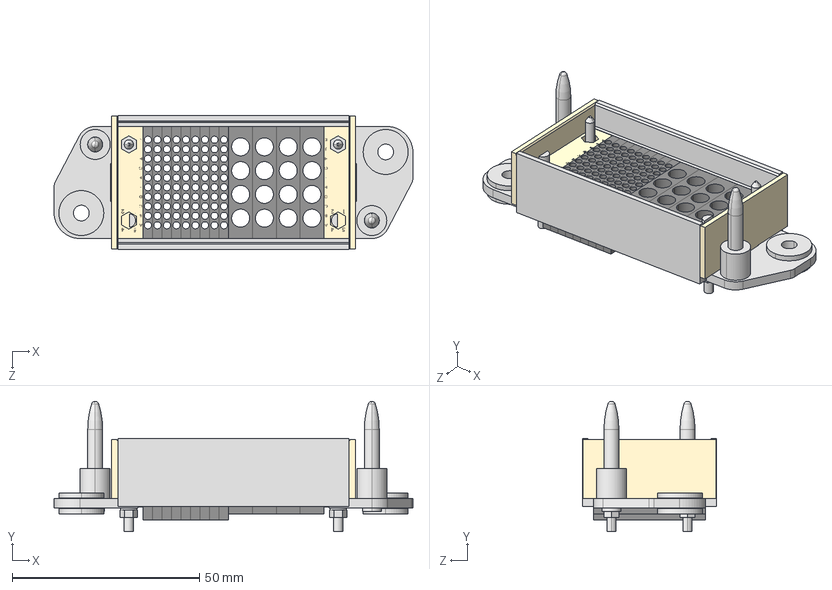
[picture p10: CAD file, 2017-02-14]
Project_QUBO/cadFiles/Hypertronics/Hypertronics3DCONFIG-NPH-NPH19_4KMR_5KMRR_4VMP1_TH.step
95.9 x 34.9 x 35.7 mm
Hypertronics3DCONFIG-NPH-NPH194KMR5KMRR4VMP1TH_NPH ENDCAP_Left
Hypertronics3DCONFIG-NPH-NPH194KMR5KMRR4VMP1TH_NPH ENDCAP_Right
Hypertronics3DCONFIG-NPH-NPH194KMR5KMRR4VMP1TH_NP-SIDE RAIL_19T
Hypertronics3DCONFIG-NPH-NPH194KMR5KMRR4VMP1TH_NP-SIDE RAIL_19B
Hypertronics3DCONFIG-NPH-NPH194KMR5KMRR4VMP1TH_N-SERIES-MODULE_NK x 9
Hypertronics3DCONFIG-NPH-NPH194KMR5KMRR4VMP1TH_N-SERIES-MODULE_NV x 4

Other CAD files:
Project_QUBO/cadFiles/Backplane/PG-TO263-7-3/TO263-7-1.igs
Project_QUBO/cadFiles/Backplane/molex-2SS_1720420206.prt
Project_QUBO/cadFiles/Backplane/molex-2V_022102021.prt
Project_QUBO/cadFiles/Backplane/molex-4RA_022122041.prt
Project_QUBO/cadFiles/Backplane/molex-4V_022102041.prt
Project_QUBO/cadFiles/Backplane/molex-6RA_022122061.prt
Project_QUBO/cadFiles/Backplane/molex-6V_022102061.prt
Project_QUBO/cadFiles/Backplane/molex-8SS_1720420806.prt

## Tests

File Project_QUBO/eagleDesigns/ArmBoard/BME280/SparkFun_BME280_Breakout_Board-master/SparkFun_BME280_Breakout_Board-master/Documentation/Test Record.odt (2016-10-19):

# Functional Test Record

Marshall Taylor

8/21/2015

HW version v02

## Testing with I2C mode

#### Test the I2C Addressing

Procedure:

1. Use ReadAllData sketch with default HW
2. Test default condition
3. Switch address jumper
4. Change address in code
5. Test alternate address

Criteria:

1. Did the modes work? YES
2. Does the silkscreen match the operation? YES

#### Signal Integrity of I2C lines

Procedure:

1. Attach scope probes to SDA and SCL with the shortest wire possible
2. Capture a full operation
3. Capture a zoom of 3 consecutively toggling SDA bits

Criteria:

1. Are I2C interface rise times are far below clk pulse high width?
2. Record the pullup resistor value as measured:
- 1: 4.692 kOhm
- 2: 4.698 kOhm

## Testing with SPI mode

Procedure:

1. Connect the BME280 to an arduino through the level shifter
2. Attach scope probes to MOSI, MISO, CS, and CLK on the BME280 side
3. Capture a full operation
4. Capture a zoom of 3 consecutively toggling data bits for MISO
5. Capture a zoom of 3 consecutively toggling data bits for MOSI

Criteria:

1. Does the clock phase and polarity match the datasheets? YES, phase defined by clk state after SS goes low
2. Include the captures.

## Power Consumption

Procedure:

1. Measure the current draw before the IC is configured
2. Configure and spam read the data
3. Measure the current draw during spam read

Criteria:

1. Are both numbers below 5mA?
2. Record both currents
- Idle: ~1.5mA
- Max: ~2.0mA

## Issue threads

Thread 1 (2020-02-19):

Power board main battery voltage sense

naterenegar, 2020-02-19:
Embedded would like to have a voltage reading on the main battery levels. This can be used to estimate the time left on our battery charge and turn off the robot in the case of a low battery.

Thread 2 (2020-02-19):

ARM Board PWM Signal Revision

naterenegar, 2020-02-19:
I would like to use the following pins for 8 PWM outputs:
PD0, PD1, PE4, PE5, PF0, PF1, PF2, PF3

See table 10-2 (pg 650) for full pinning information on the tiva:
[http://www.ti.com/lit/ds/symlink/tm4c123gh6pm.pdf](url)

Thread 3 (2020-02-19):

ARM Board USB input

naterenegar, 2020-02-19:
I'd like to connect the AHRS via USB to our tiva. This could be done in a couple of ways, but I think the easiest is to modify the ARM board to have a female USB connector. I can comment later with pin information.

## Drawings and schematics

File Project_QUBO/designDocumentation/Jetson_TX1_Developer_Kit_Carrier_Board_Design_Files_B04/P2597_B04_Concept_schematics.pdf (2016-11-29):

# Block Diagram

P2597-B04

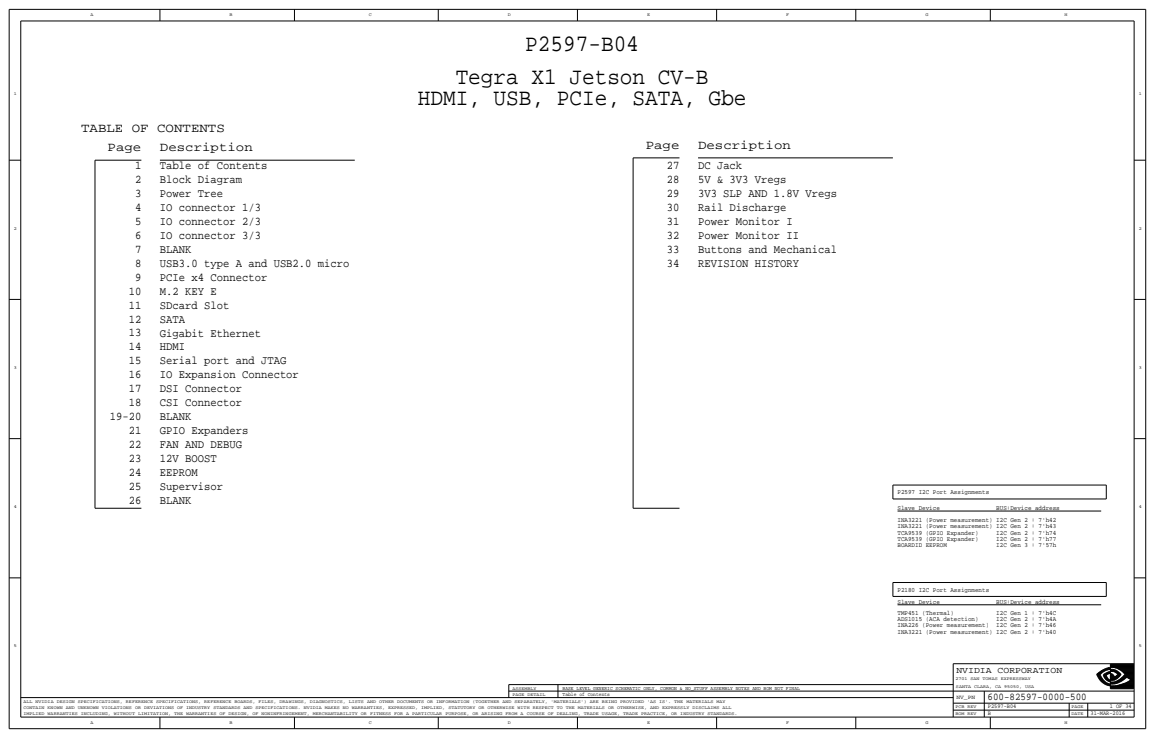
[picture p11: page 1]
Slave Device; BUS:Device address; TCA9539 (GPIO Expander); I2C Gen 2 : 7'h74; I2C Gen 2 : 7'h77; BOARDID EEPROM; I2C Gen 3 : 7'57h; TMP451 (Thermal); I2C Gen 1 : 7'h4C; ADS1015 (ACA detection); I2C Gen 2 : 7'h4A; Serial port and JTAG; IO connector 1/3; Power Monitor II Buttons and Mechanical; SDcard Slot; IO Expansion Connector; Supervisor; EEPROM; USB3.0 type A and USB2.0 micro; BLANK; IO connector 3/3; IO connector 2/3; FAN AND DEBUG; CSI Connector; DSI Connector; Table of Contents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

Tegra X1 Jetson CV-B
HDMI, USB, PCIe, SATA, Gbe

P2597 I2C Port Assignments
INA3221 (Power measurement) I2C Gen 2 : 7'h42
INA3221 (Power measurement) I2C Gen 2 : 7'h43

P2180 I2C Port Assignments
INA226 (Power measurement) I2C Gen 2 : 7'h46
INA3221 (Power measurement) I2C Gen 2 : 7'h40

NVIDIA CORPORATION 2701 SAN TOMAS EXPRESSWAY SANTA CLARA, CA 95050, USA

ASSEMBLY | BASE LEVEL GENERIC SCHEMATIC ONLY, COMMON & NO_STUFF ASSEMBLY NOTES AND BOM NOT FINAL
PAGE DETAIL | Table of Contents | NV_PN | 600-82597-0000-500

ALL NVIDIA DESIGN SPECIFICATIONS, REFERENCE SPECIFICATIONS, REFERENCE BOARDS, FILES, DRAWINGS, DIAGNOSTICS, LISTS AND OTHER DOCUMENTS OR INFORMATION (TOGETHER AND SEPARATELY, 'MATERIALS') ARE BEING PROVIDED 'AS IS'. THE MATERIALS MAY
CONTAIN KNOWN AND UNKNOWN VIOLATIONS OR DEVIATIONS OF INDUSTRY STANDARDS AND SPECIFICATIONS. NVIDIA MAKES NO WARRANTIES, EXPRESSED, IMPLIED, STATUTORY OR OTHERWISE WITH RESPECT TO THE MATERIALS OR OTHERWISE, AND EXPRESSLY DISCLAIMS ALL
IMPLIED WARRANTIES INCLUDING, WITHOUT LIMITATION, THE WARRANTIES OF DESIGN, OF NONINFRINGEMENT, MERCHANTABILITY OR FITNESS FOR A PARTICULAR PURPOSE, OR ARISING FROM A COURSE OF DEALING, TRADE USAGE, TRADE PRACTICE, OR INDUSTRY STANDARDS.

PCB REV | P2597-B04 | PAGE
BOM REV | B | DATE | 31-MAR-2016

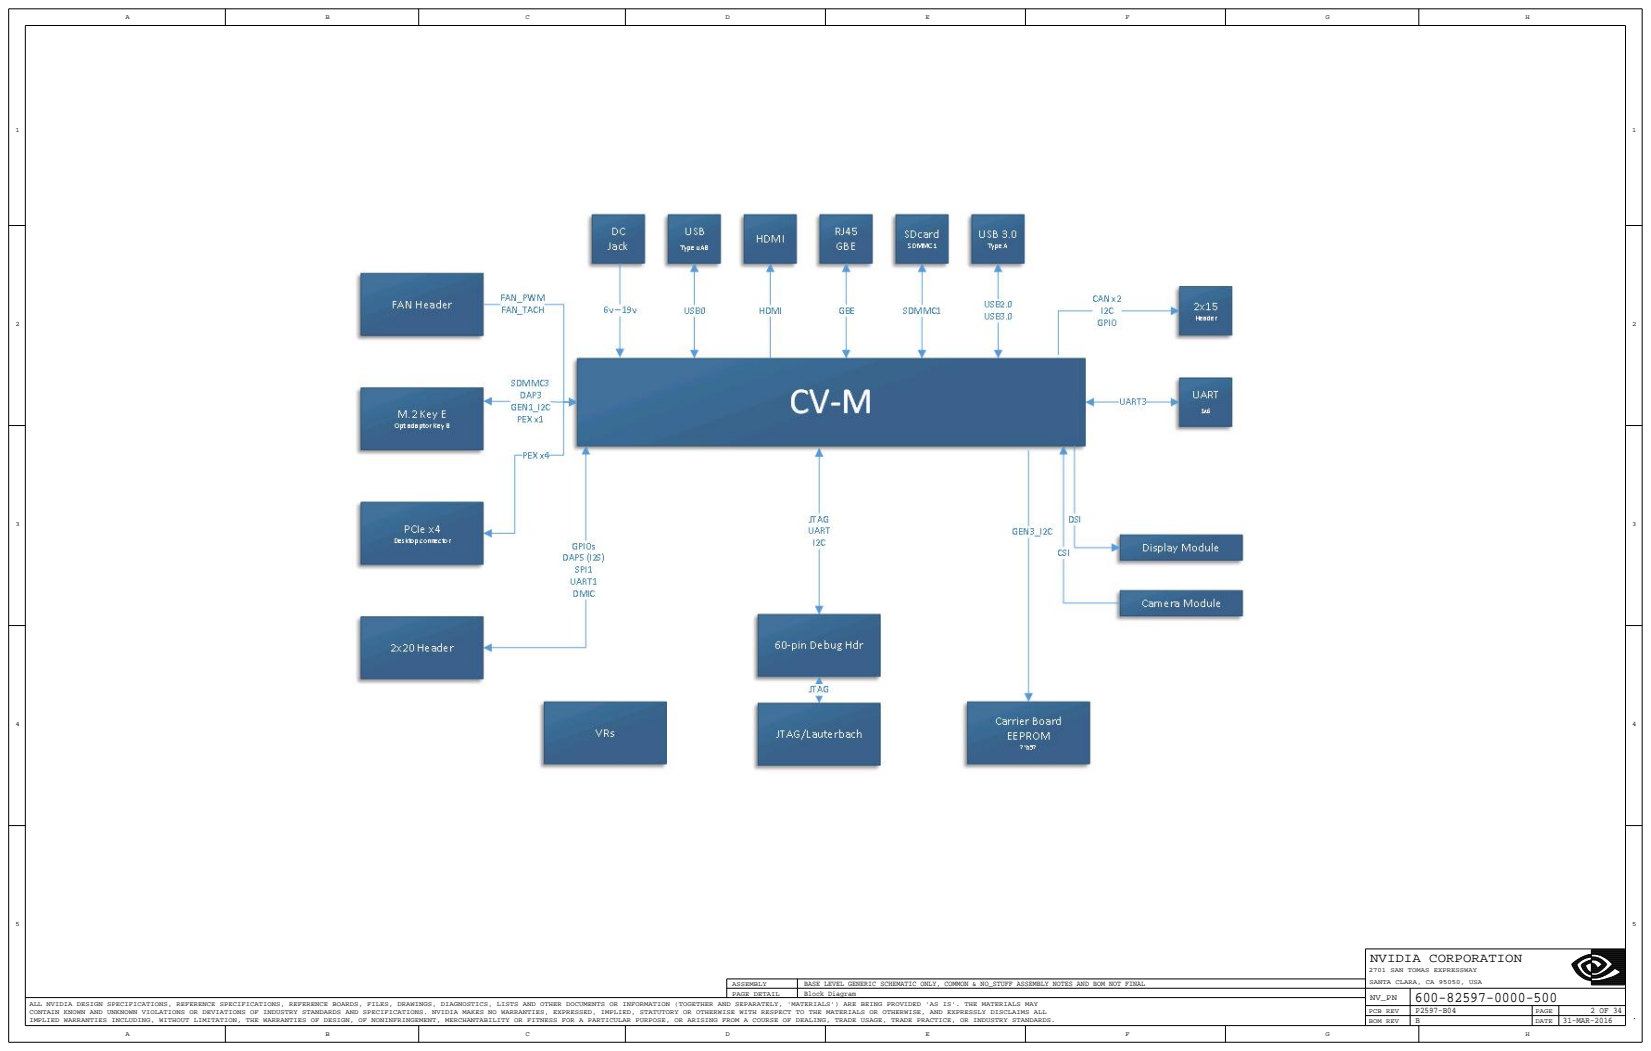
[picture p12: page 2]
CONTAIN KNOWN AND UNKNOWN VIOLATIONS OR DEVIATIONS OF INDUSTRY STANDARDS AND SPECIFICATIONS. NVIDIA MAKES NO WARRANTIES, EXPRESSED, IMPLIED, STATUTORY OR OTHERWISE WITH RESPECT TO THE MATERIALS OR OTHERWISE, AND EXPRESSLY DISCLAIMS ALL; PAGE

NVIDIA CORPORATION 2701 SAN TOMAS EXPRESSWAY

Block Diagram

# Power Tree

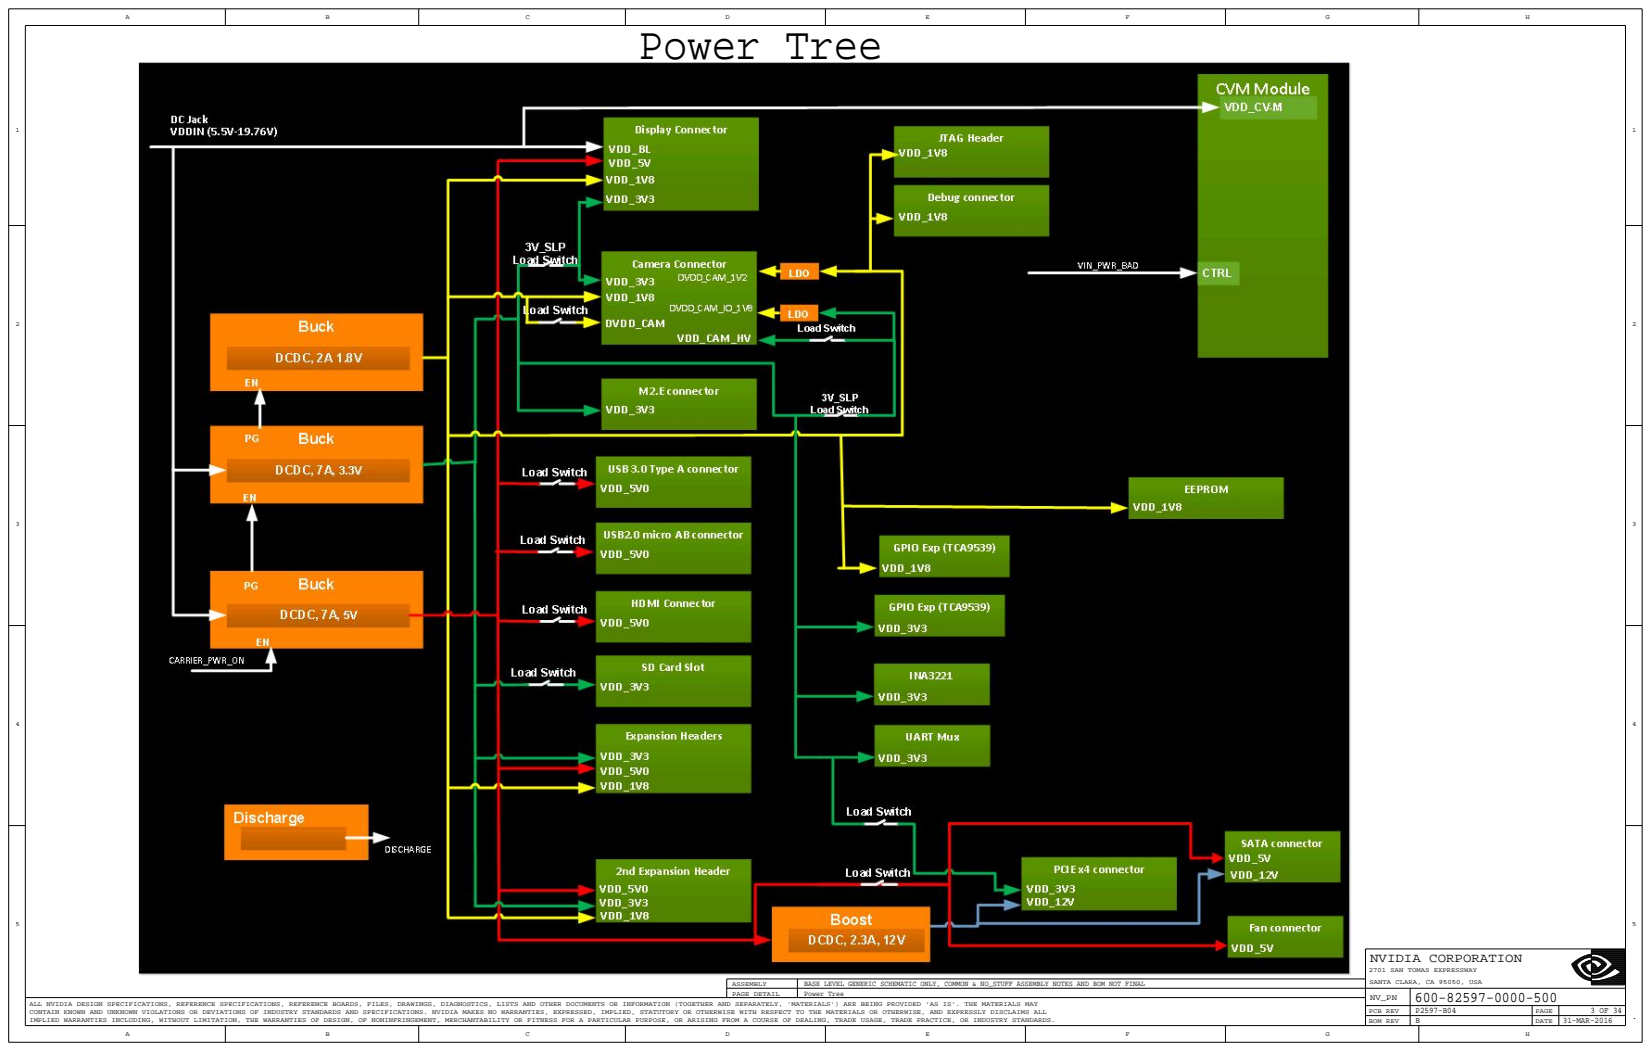
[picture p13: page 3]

NVIDIA CORPORATION 2701 SAN TOMAS EXPRESSWAY

Power Tree

## RSVD

## DAP 1 (Tegra X1)

A37 | B6 I2C_PM_DAT BI

B3 | BI
B31 | A20 I2C_GP1_DAT_3V3 BI
B41 | C10 I2C_GP2_DAT | OUT
B44 | BI
C3 C4 | C13 I2C_GP3_DAT | OUT BI

D38 | A36 IN USB0_ID_IO_CONN
D41 | IN

E40 E43 | FAN_TACH | OUT

G29 G32 | G14 MOTION_INT_AP_L A23 IN
G35 | GPIO_EXP0_INT A22 IN
G38 | GPIO_EXP1_INT IN F12 F11

FTSH-107-01-L-DV-K-P-TR MALE

G47 | 50OHM_NETCLASS2 E11 | DIRECTDC_IN
G50 H19 | E12 50OHM_NETCLASS2 | DIRECTDC_OUT0
H22 | D11 50OHM_NETCLASS2 | DIRECTDC_OUT2
H25 | D12 | DIRECTDC_OUT3

50OHM_NETCLASS2 | DIRECTDC_OUT1

H34 H37 | B11 50OHM_NETCLASS2 JTAG_AP_TCK B12 IN
H40 | 50OHM_NETCLASS2 JTAG_AP_TDI IN
H46 | B13 IN 50OHM_NETCLASS2 JTAG_AP_TRST_L
H49 | A11 NVJTAG_SEL IN

NVIDIA CORPORATION 2701 SAN TOMAS EXPRESSWAY

IO connector 1/3

J13

## CON_CVB_1_0

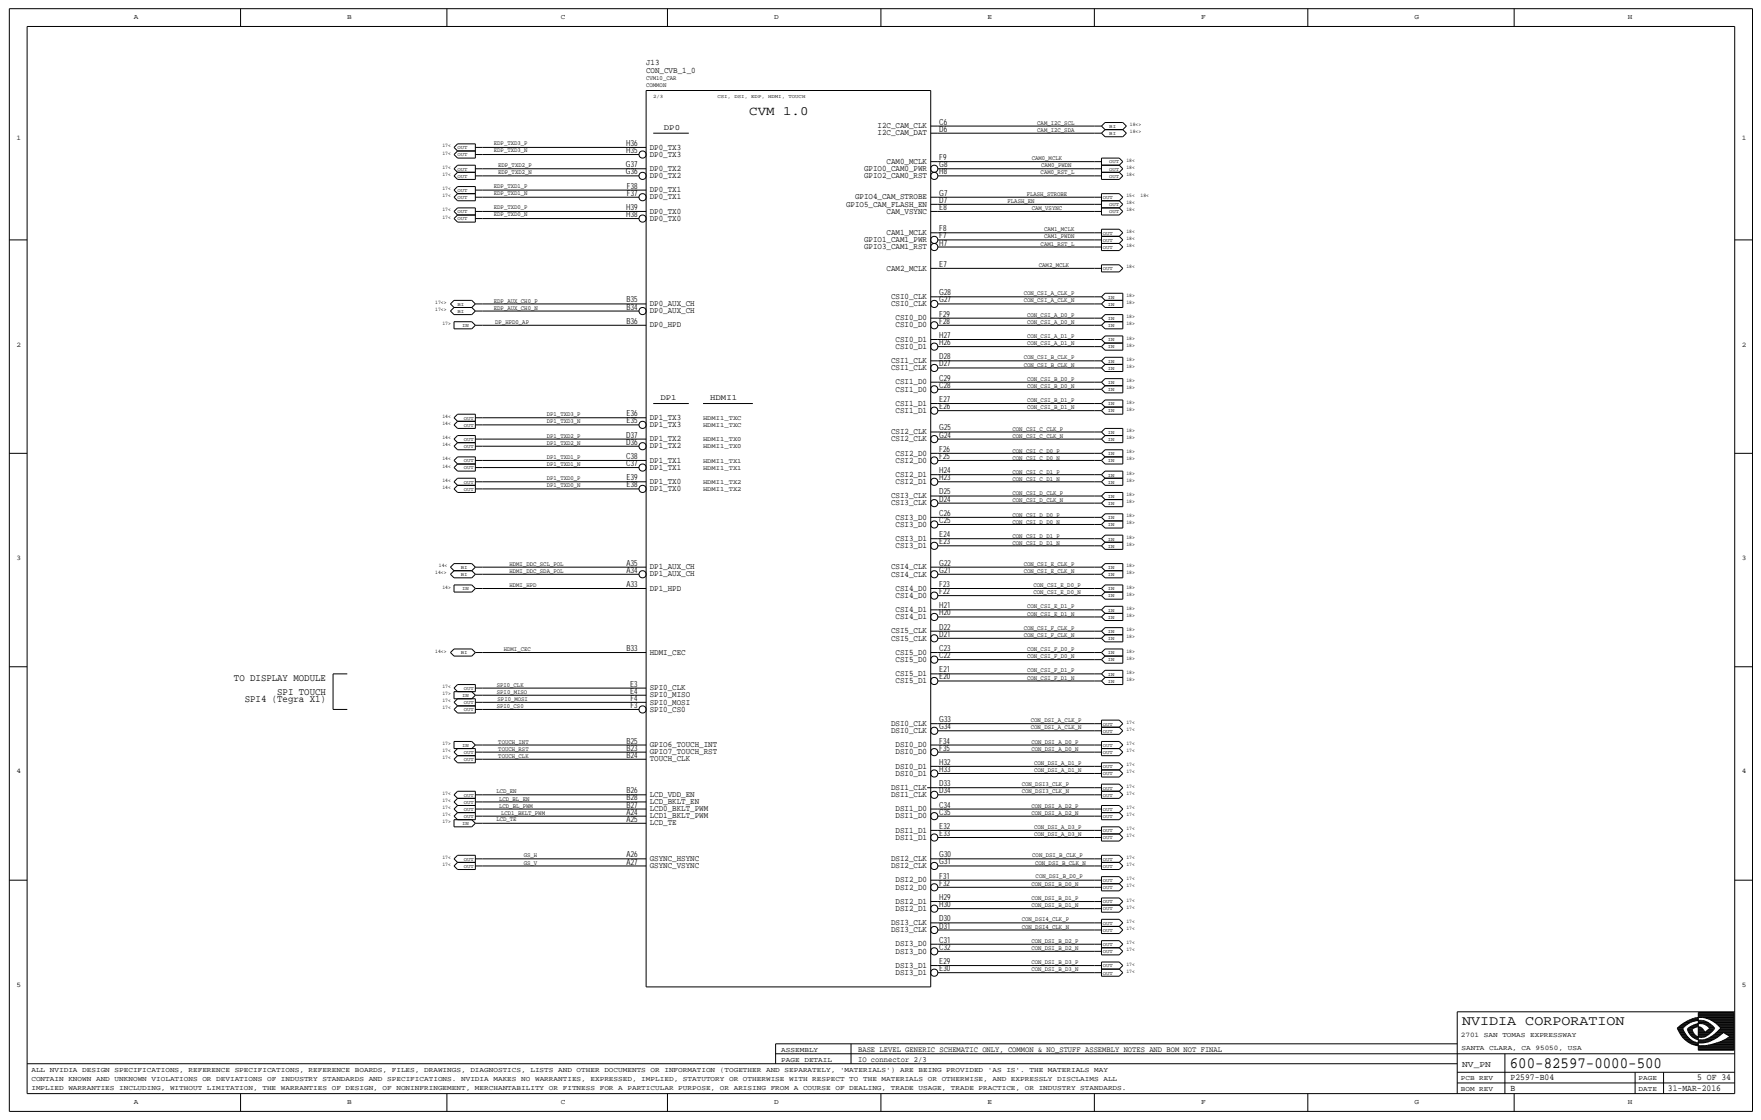
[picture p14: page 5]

IN HDMI_CEC B33 | IN

IN B23 TOUCH_RST | OUT

NVIDIA CORPORATION 2701 SAN TOMAS EXPRESSWAY

IO connector 2/3

## TO X4 PCIE PEX_CLK0 is PEX_CLK1 on Tegra X1

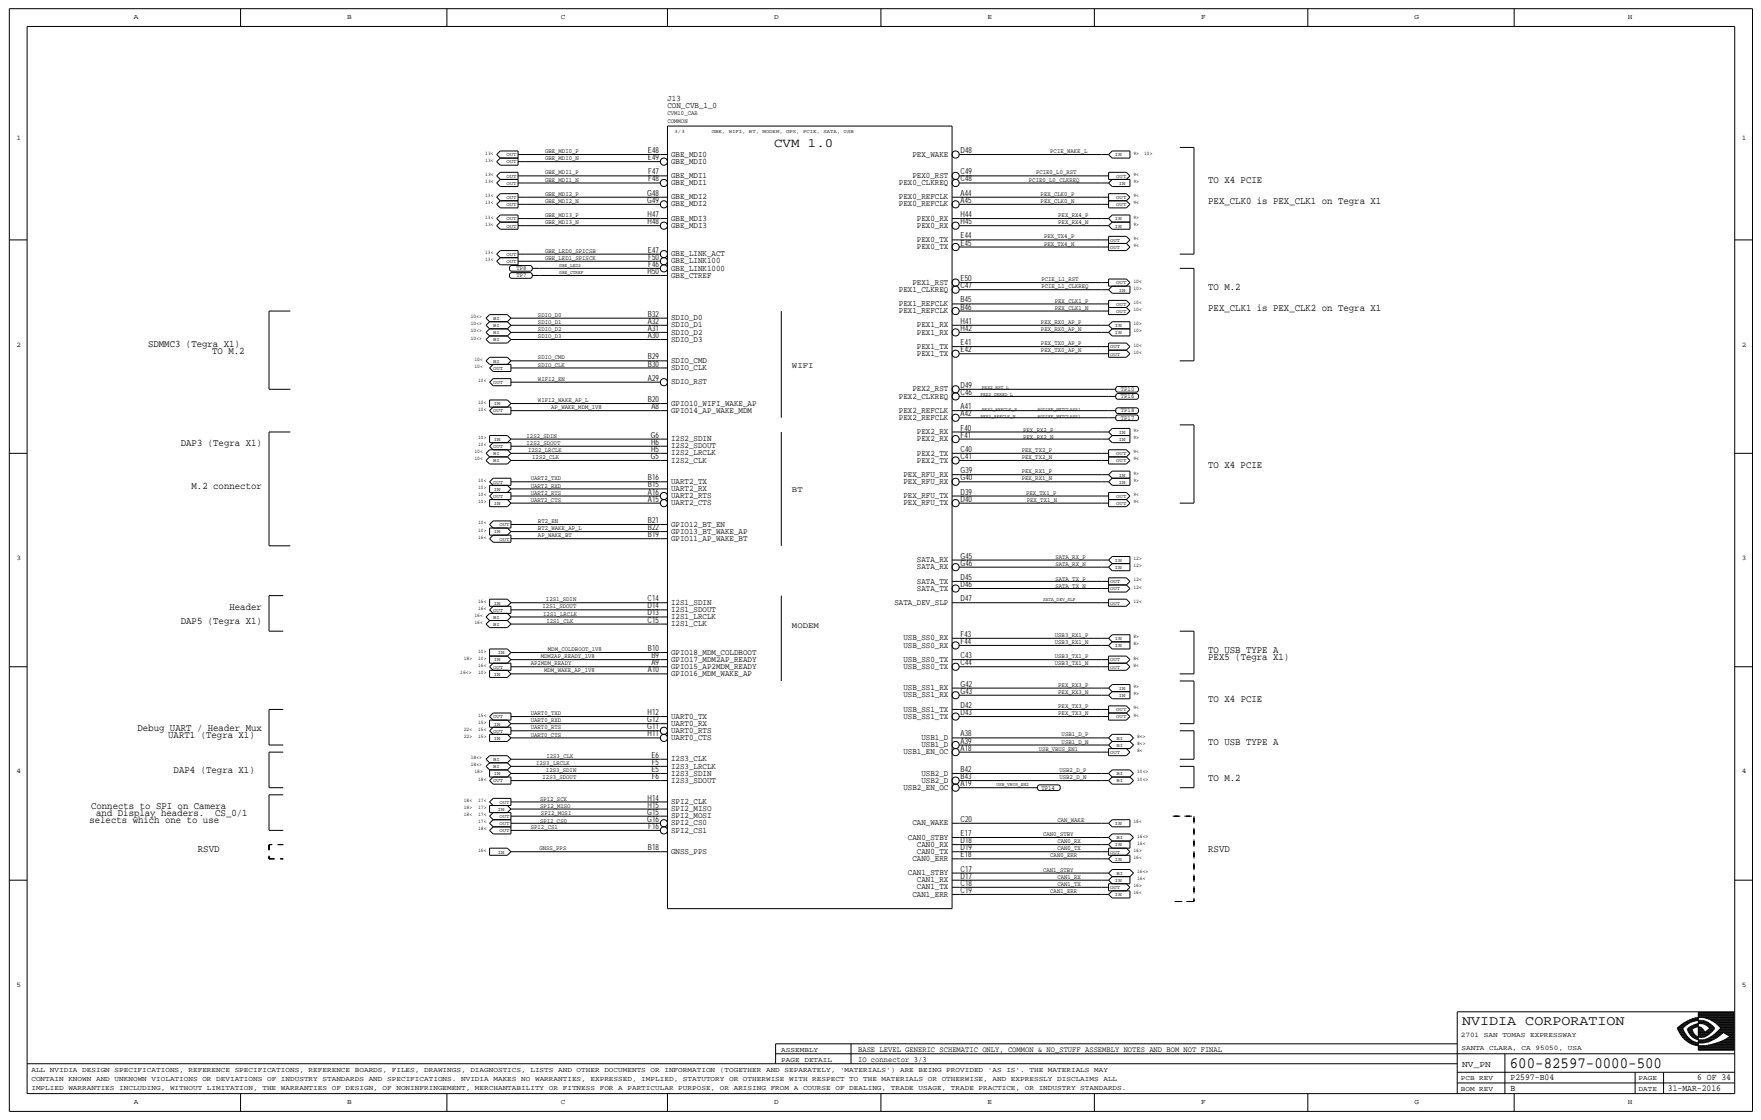
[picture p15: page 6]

TP8 H50 TP7 GBE_CTREF | IN

Debug UART / Header Mux UART1 (Tegra X1)

I2S3_SDIN IN | BI

Connects to SPI on Camera
and Display headers. CS_0/1
selects which one to use

NVIDIA CORPORATION 2701 SAN TOMAS EXPRESSWAY

IO connector 3/3

# BLANK

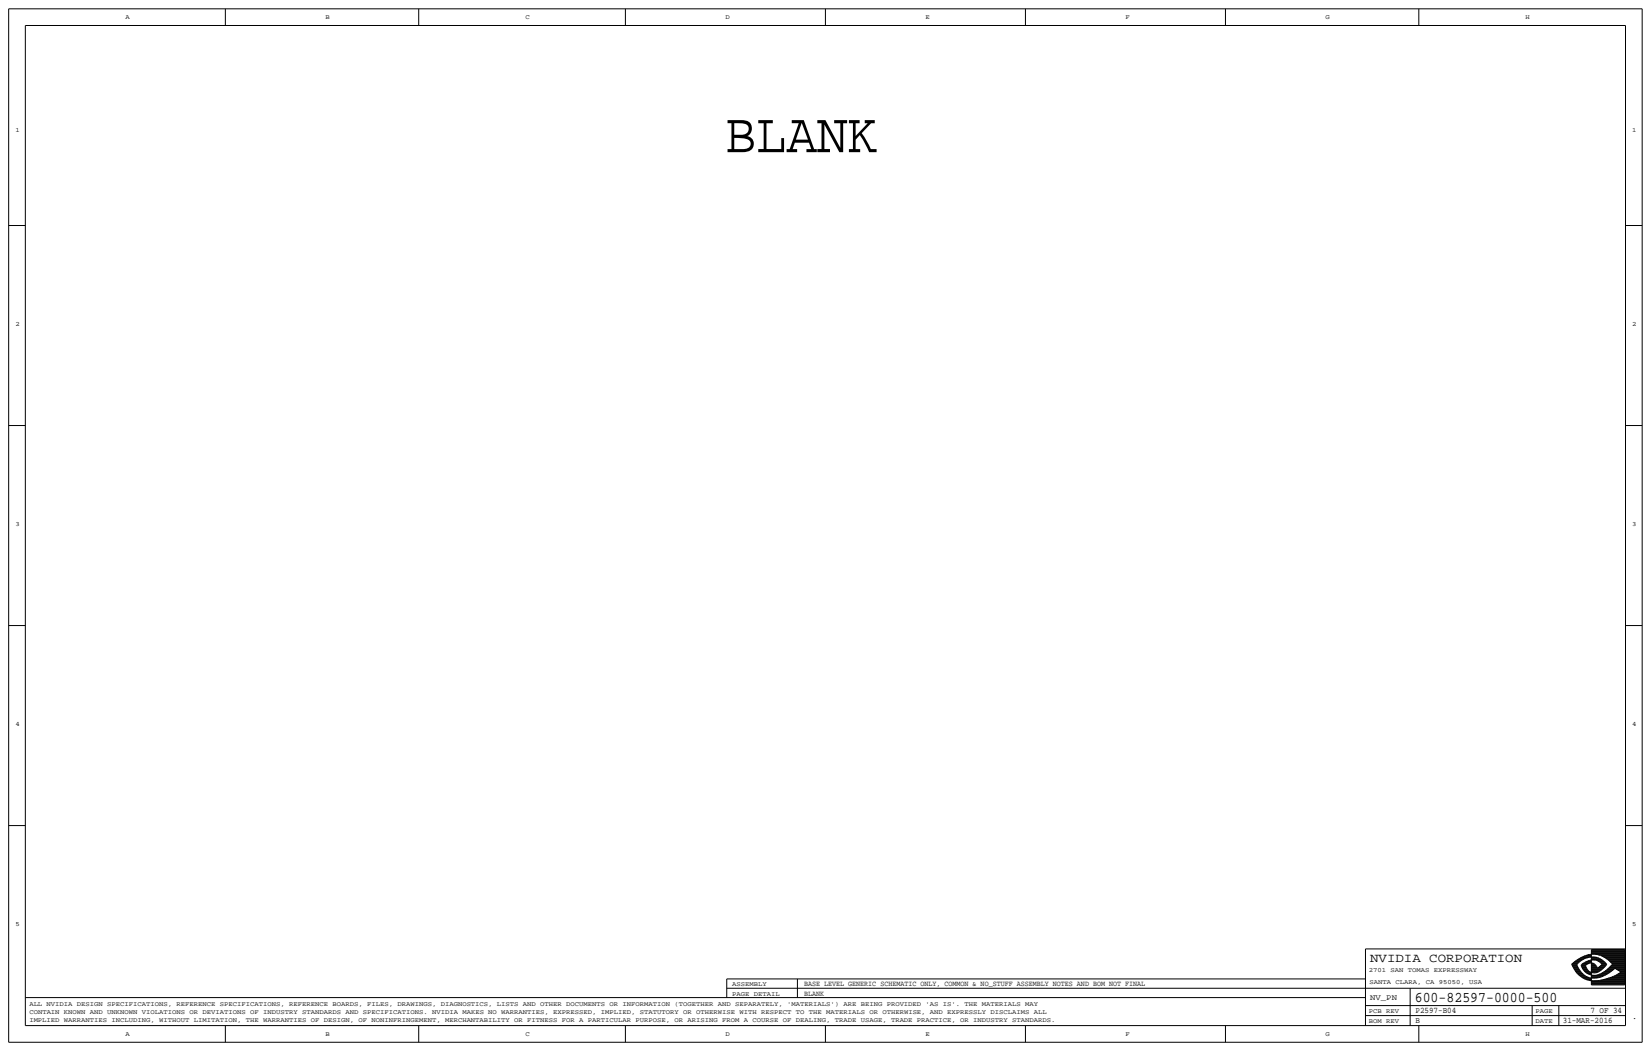
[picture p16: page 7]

NVIDIA CORPORATION 2701 SAN TOMAS EXPRESSWAY

BLANK

### Co-locate Resistors to avoid stubs

# USB 3.0 TYPE A CONNECTOR

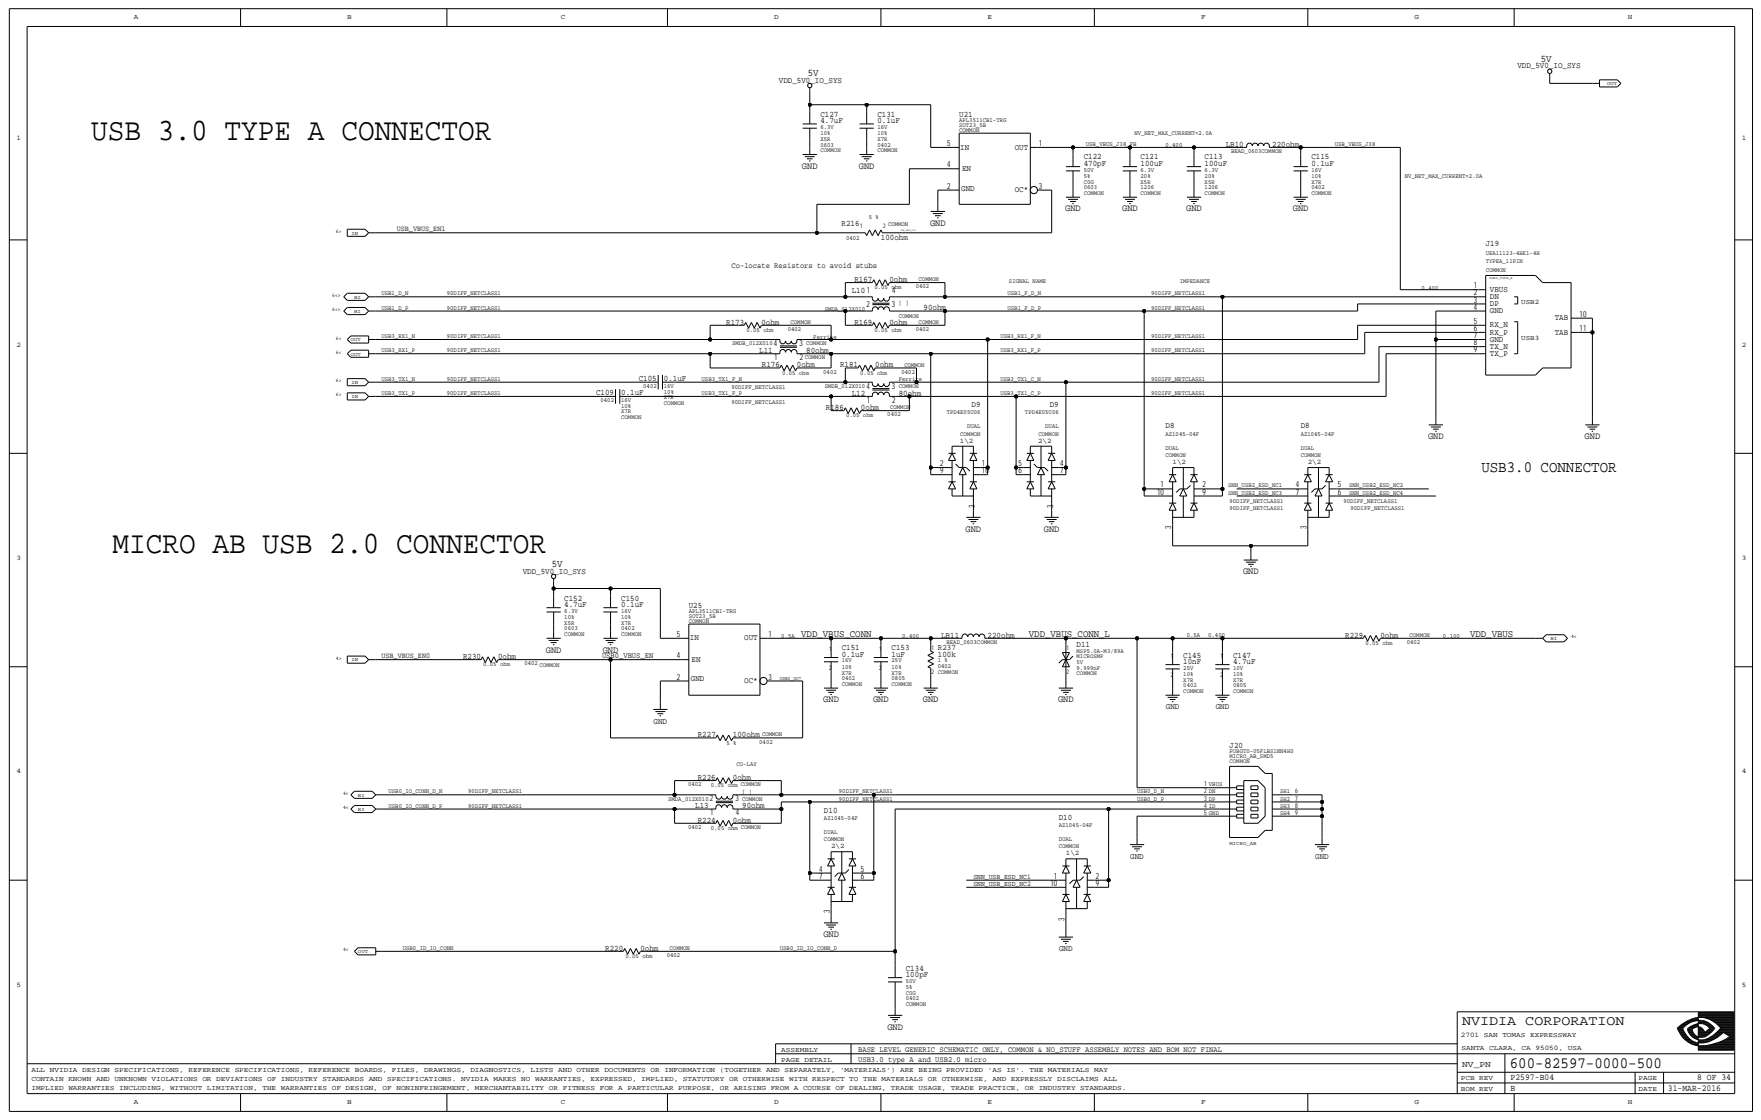
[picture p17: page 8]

MICRO AB USB 2.0 CONNECTOR

NVIDIA CORPORATION 2701 SAN TOMAS EXPRESSWAY

USB3.0 type A and USB2.0 micro

R349 1

CR6 2

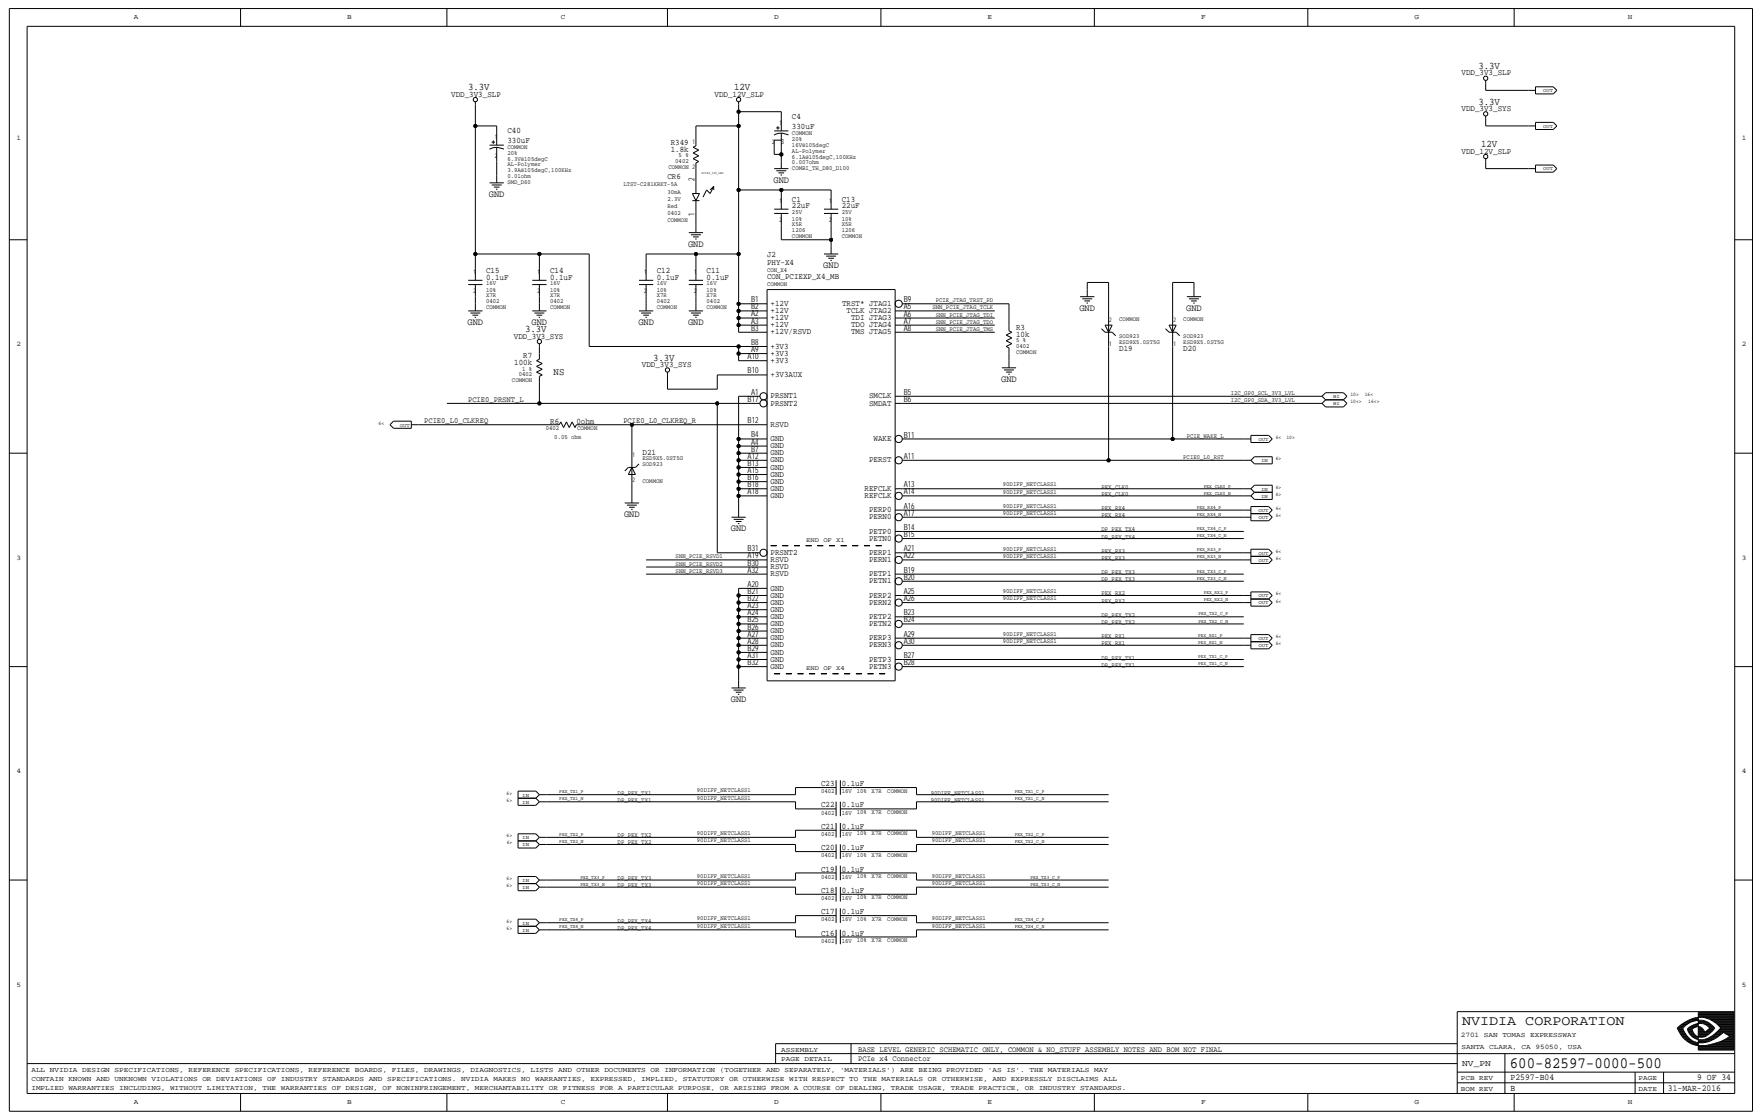
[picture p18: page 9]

A18 | IN
A19 | IN

B22 | B23 DP_PEX_TX2 PEX_TX2_C_P B24 DP_PEX_TX2 PEX_TX2_C_N | OUT
A23 | | OUT

A28 | OUT
B29 | OUT

NVIDIA CORPORATION 2701 SAN TOMAS EXPRESSWAY

PCIe x4 Connector

# M.2 KEY E

## +/-5% 2Amps

MDM_EN_R 48 46 MDM_RST_R_L | 49 47 | IN PEX_CLK1_P

I2C_GP0_SDA_3V3_LVL | 5 | | 4 | I2C_GP0_DAT_1V8

NVIDIA CORPORATION 2701 SAN TOMAS EXPRESSWAY

M.2 KEY E

# SD CARD SOCKET

U503

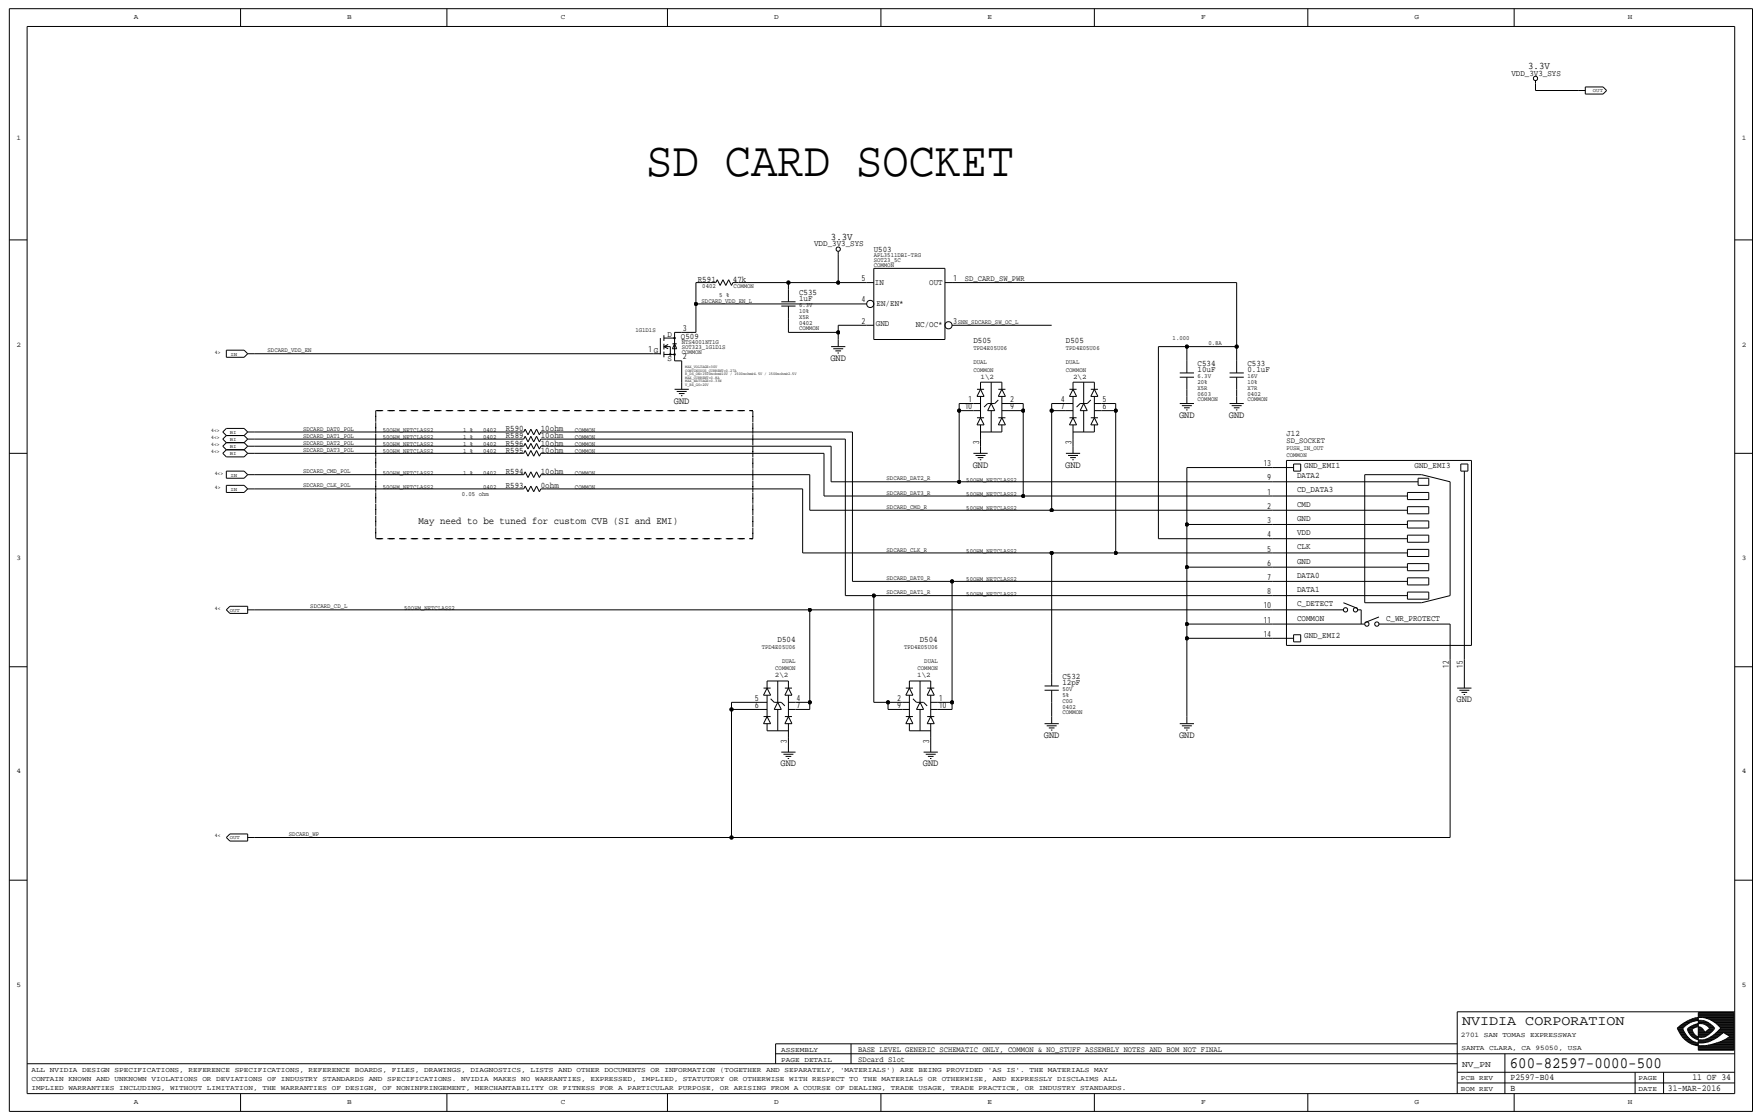
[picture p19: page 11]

SDCARD_CMD_R | 2 | CMD
SDCARD_CLK_R | 3 | GND

4 | VDD
5 | CLK

SDCARD_DAT0_R | 6 | GND

7 | DATA0

NVIDIA CORPORATION 2701 SAN TOMAS EXPRESSWAY

SDcard Slot

# SATA Connector

## VDD_3V3_SLP

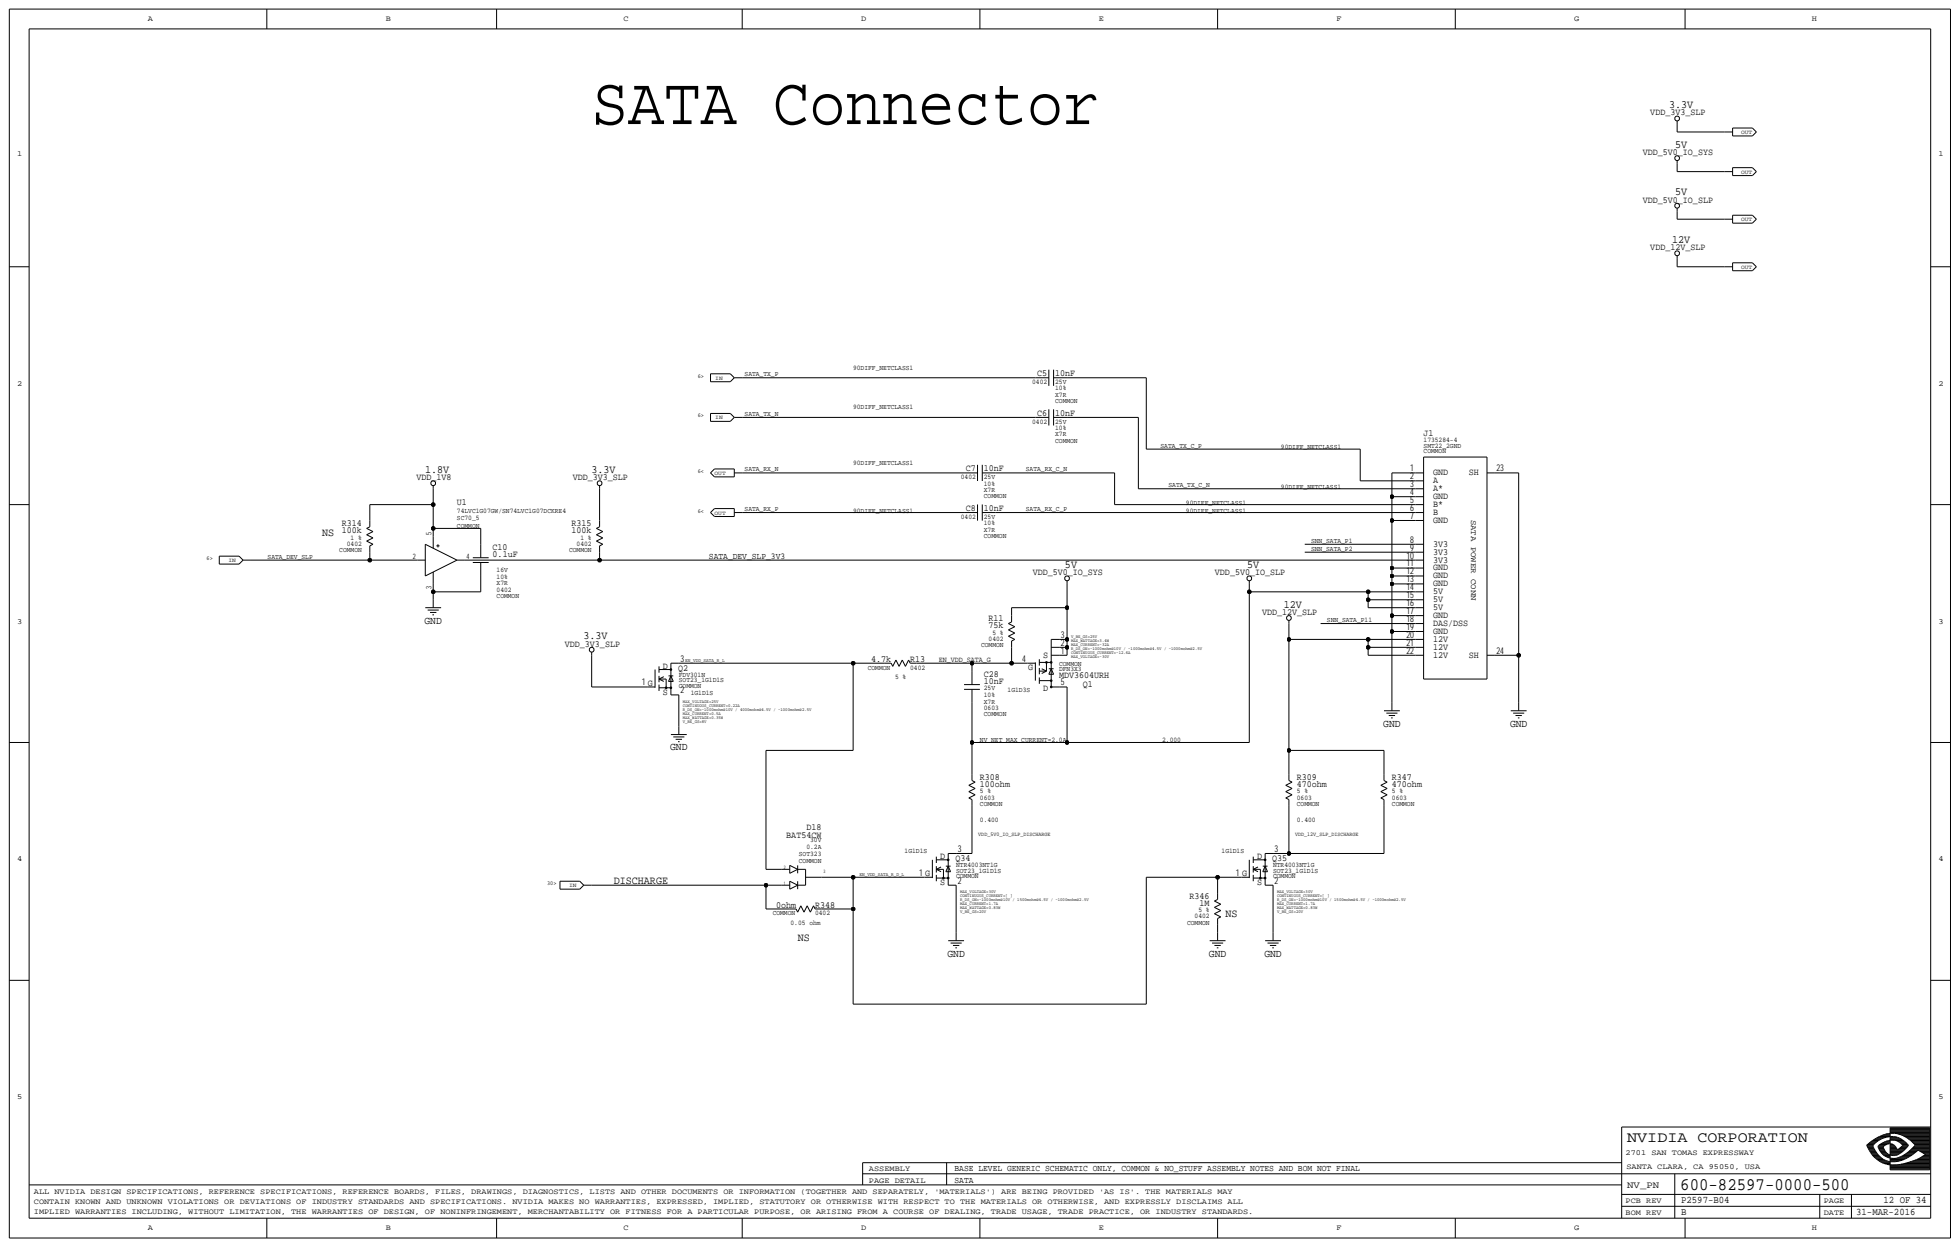
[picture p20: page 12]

IN | 10% X7R COMMON

NVIDIA CORPORATION 2701 SAN TOMAS EXPRESSWAY

SATA
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

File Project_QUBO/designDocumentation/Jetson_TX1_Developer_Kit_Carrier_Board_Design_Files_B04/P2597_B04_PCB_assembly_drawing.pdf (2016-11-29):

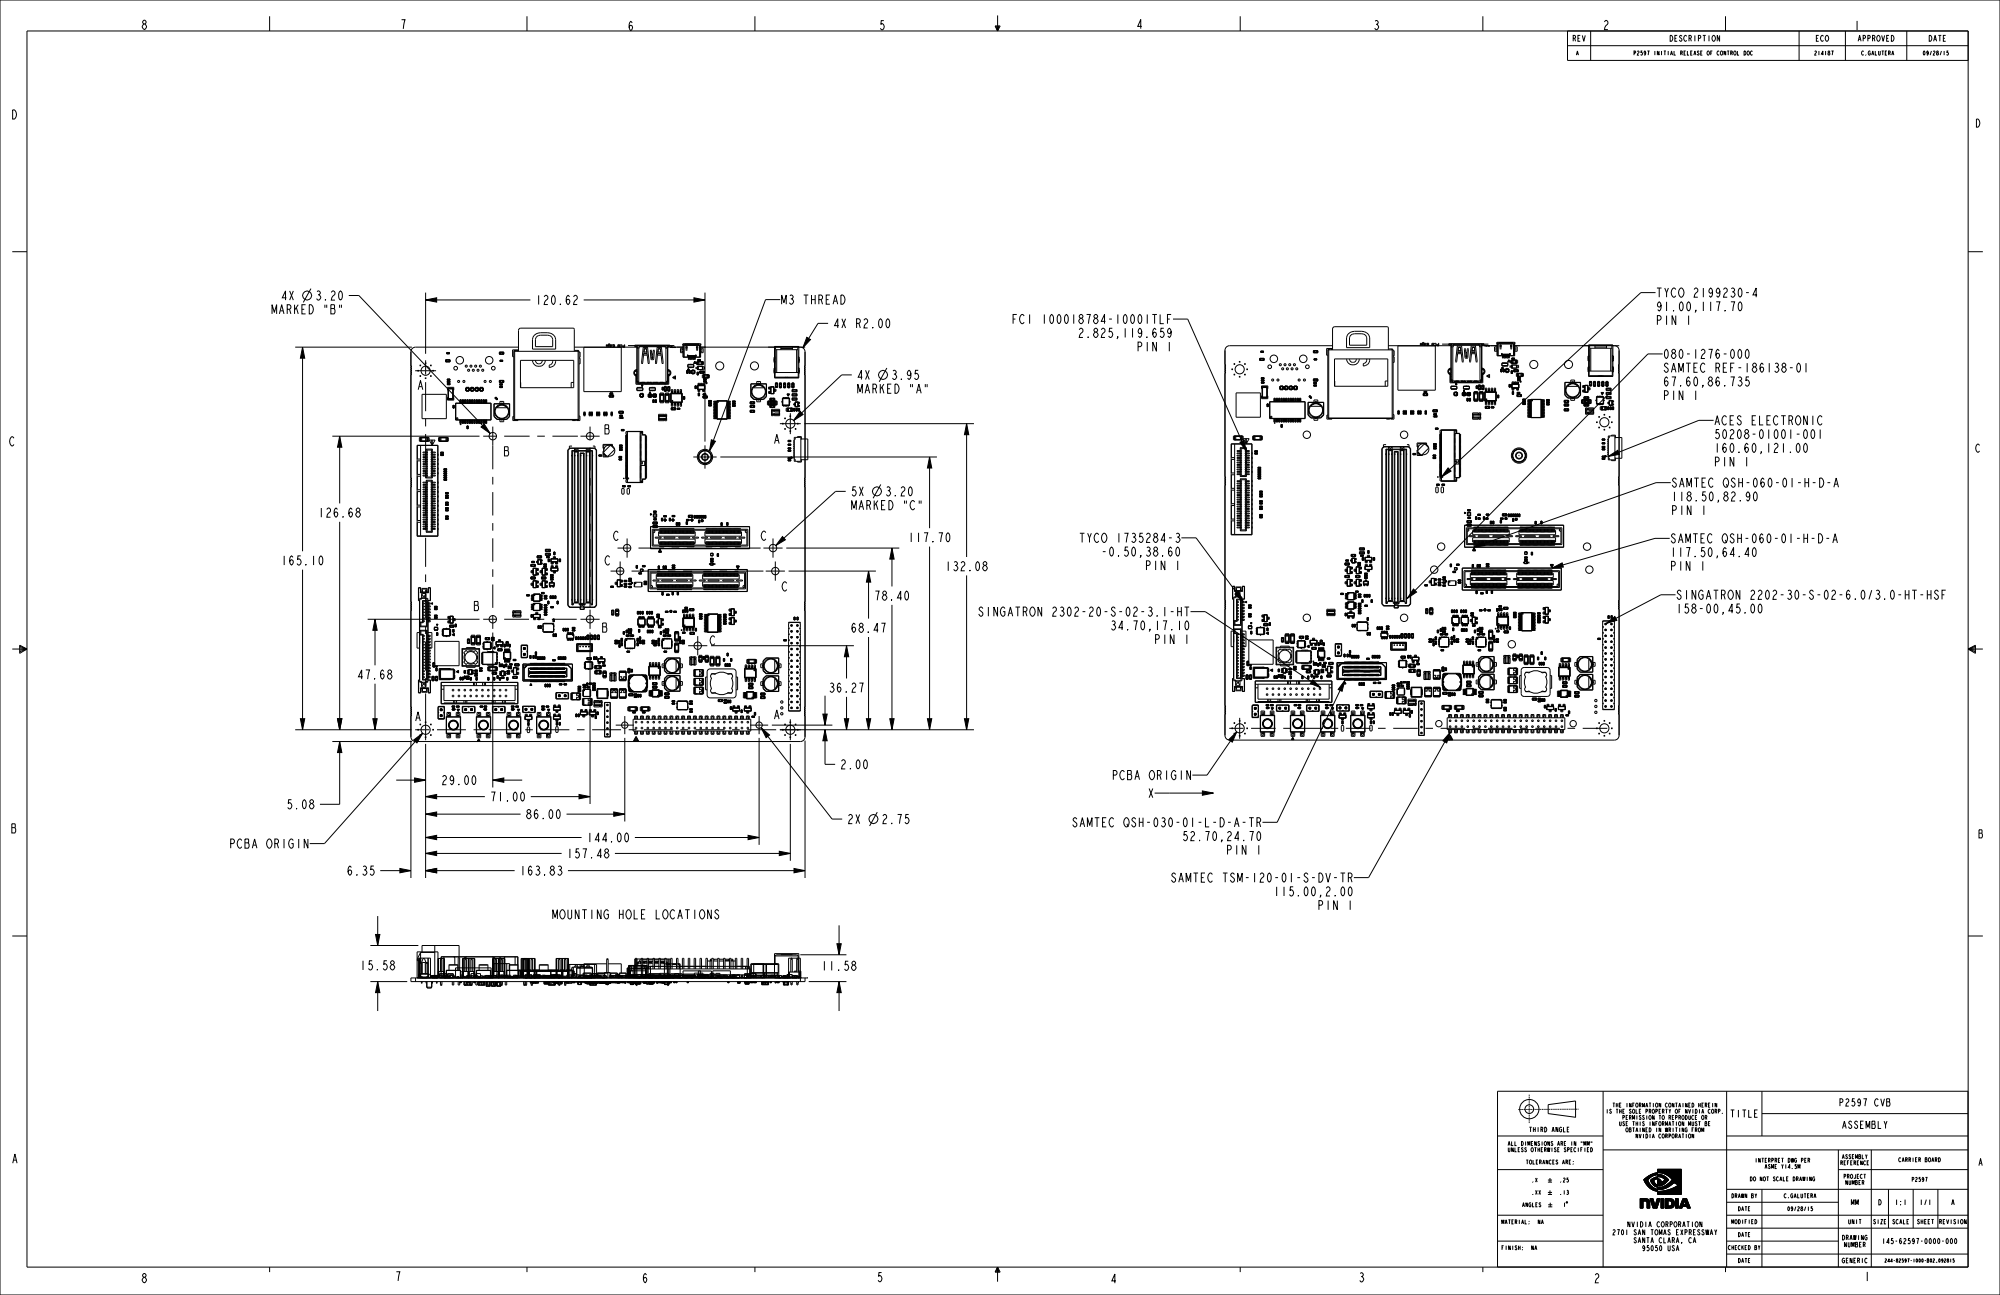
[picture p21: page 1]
THIRD ANGLE; 4X MARKED "A"; 120.62 4X MARKED "B"; 5X MARKED "C"; REV; DESCRIPTION; ECO; APPROVED; DATE; P2597 INITIAL RELEASE; CONTROL; DOC; C.GALUTERA; FINISH: NA; GENERIC; NUMBER; MATERIAL: NA; MODIFIED; UNIT; SIZE; SCALE; SHEET; REVISION; ANGLES; DRAWN BY; ASME; DO NOT SCALE; DRAWING; PROJECT; ALL DIMENSIONS ARE; UNLESS OTHERWISE; SPECIFIED; TOLERANCES ARE:; ASSEMBLY; REFERENCE; CARRIER BOARD; THE; INFORMATION CONTAINED HEREIN; THE SOLE PROPERTY OF; NVIDIA CORP.; PERMISSION TO REPRODUCE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

SAMTEC QSH-030-01-L-D-A-TR

PIN 1
SAMTEC TSM-120-01-S-DV-TR

MOUNTING HOLE LOCATIONS

OBTAINED IN WRITING FROM
NVIDIA CORPORATION

INTERPRET DWG PER

2701 SAN TOMAS EXPRESSWAY
SANTA CLARA, CA
95050 USA

DRAWING

CHECKED BY

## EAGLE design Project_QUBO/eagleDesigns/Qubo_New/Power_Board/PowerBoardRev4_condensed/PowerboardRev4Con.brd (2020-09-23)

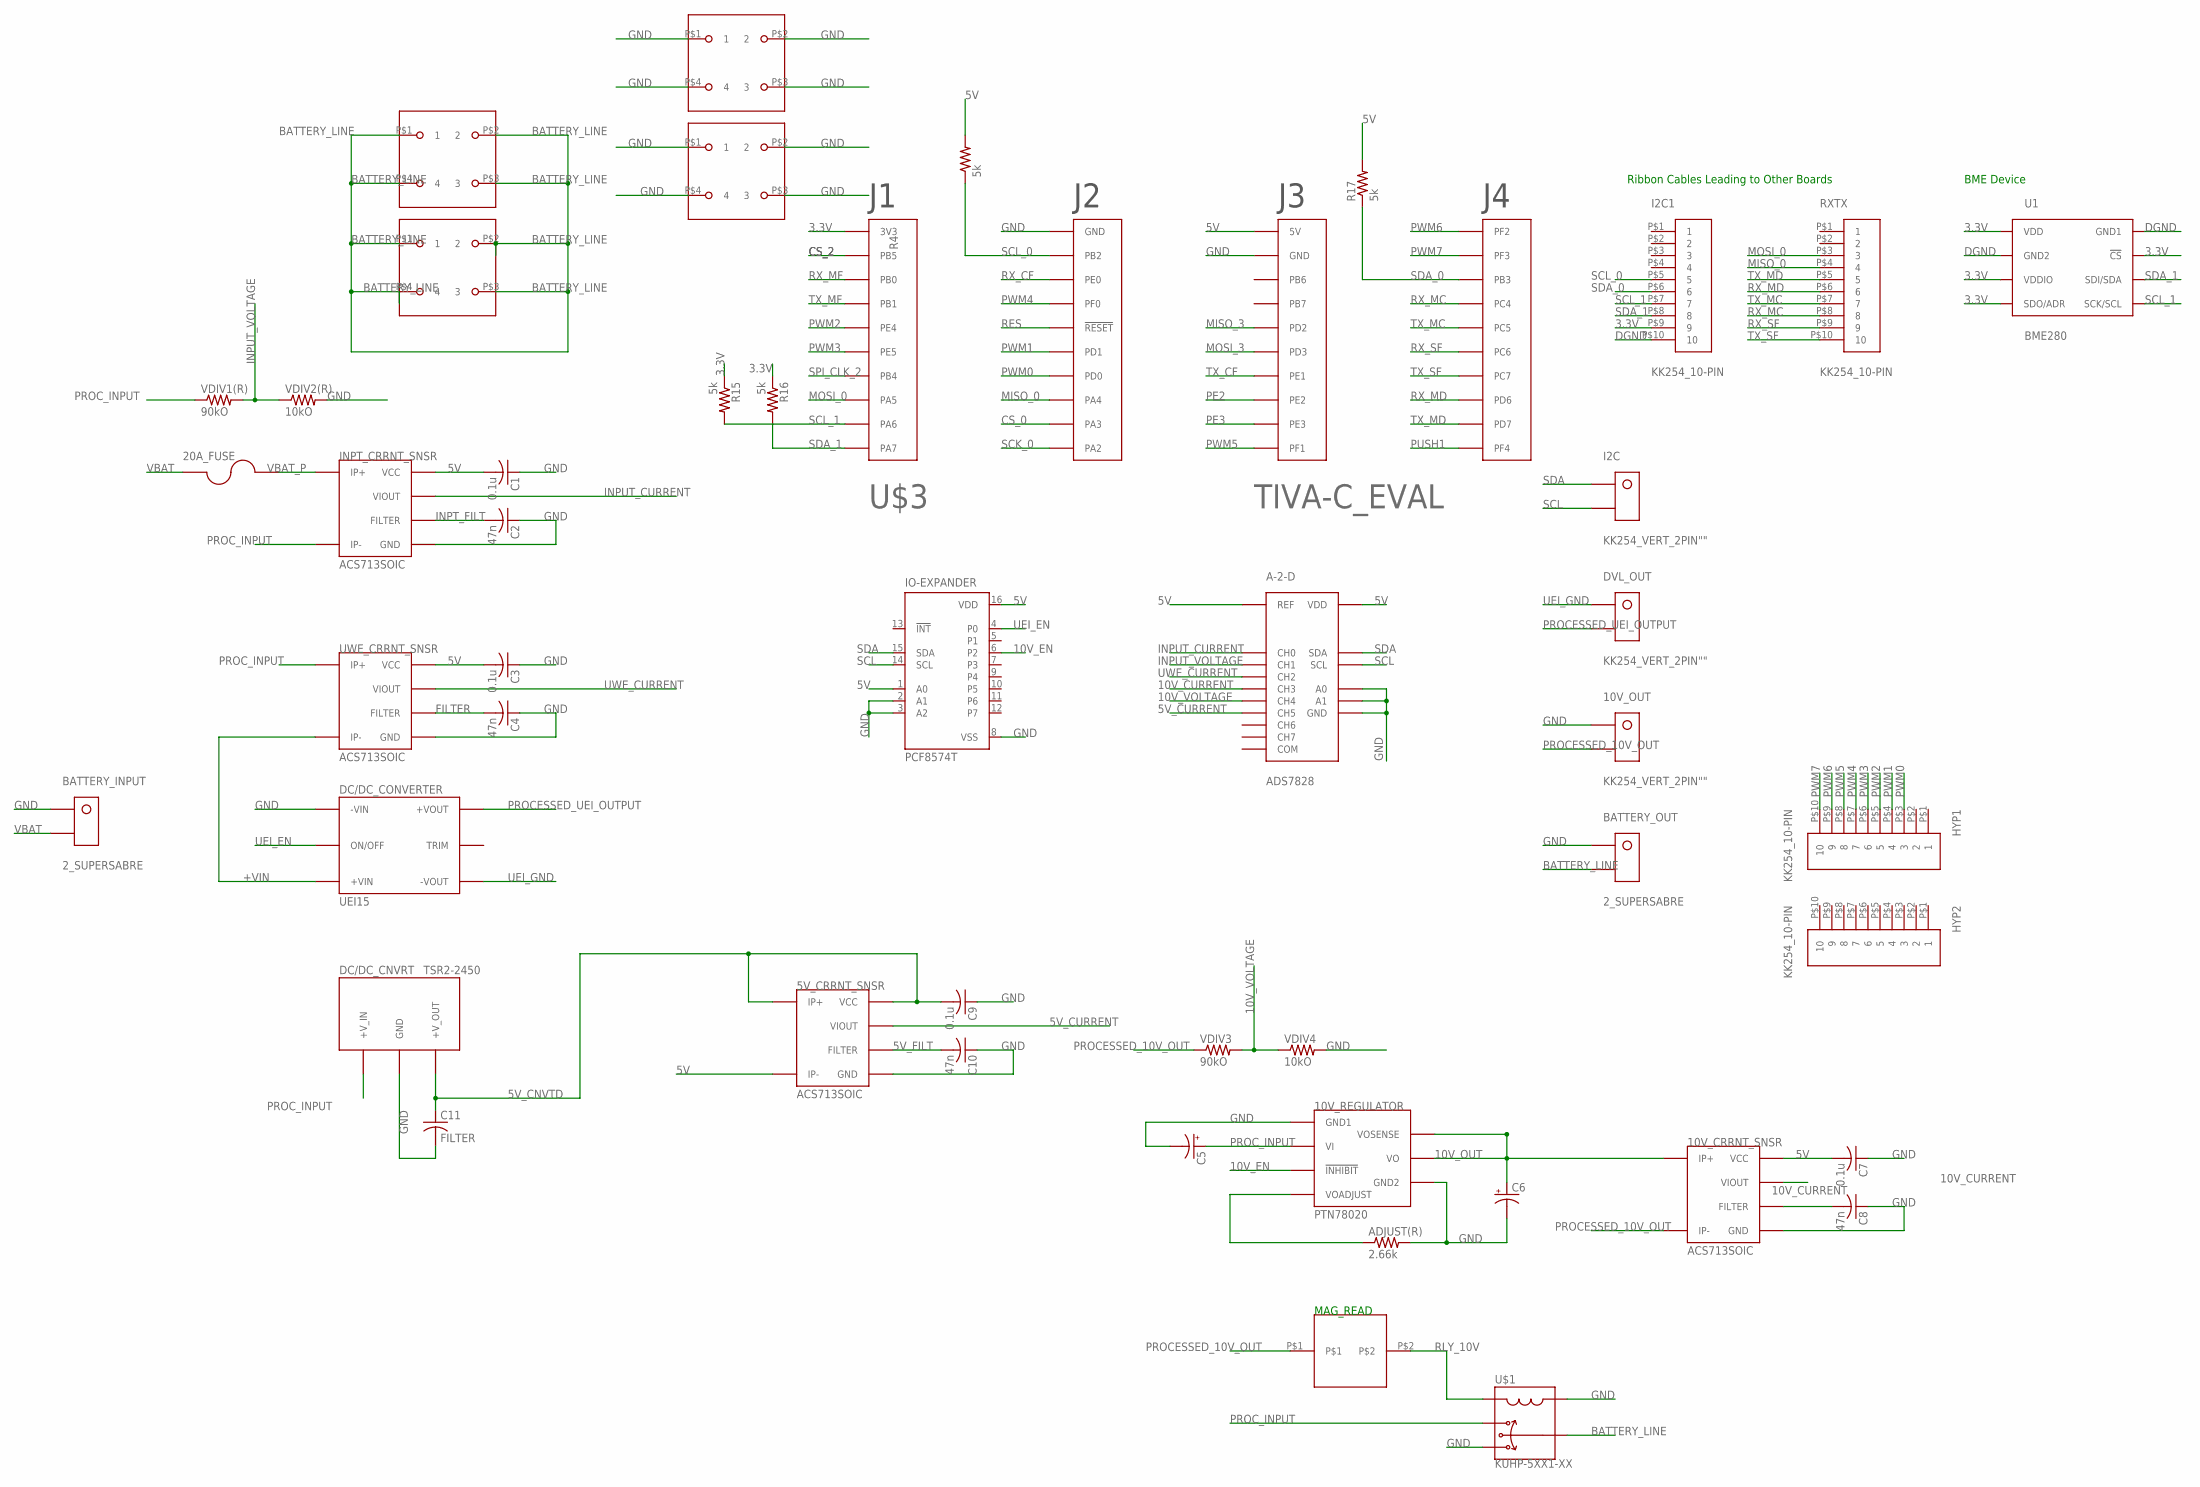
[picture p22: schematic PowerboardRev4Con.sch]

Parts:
5V_CRRNT_SNSR, 10V_CRRNT_SNSR: ACS713SOIC; ACS713-SOIC
10V_OUT: KK254_VERT_2PIN""; KK254_VERT_2PIN
10V_REGULATOR: PTN78020; PTN
20A_FUSE: BOWED-1.25"-FUSECLIPS; 1.25"_FUSECLIPS
A-2-D: ADS7828; TSSOP16
ADJUST(R): 2.66k; R0805
BATTERY_INPUT: 2_SUPERSABRE; SUPERSABRE_2CIRCUIT
BATTERY_OUT: 2_SUPERSABRE; SUPERSABRE_2CIRCUIT
C1, C3, C7, C9: 0.1u; C0805
C2, C4, C8, C10: 47n; C0805
C5, C6: CPOL-US; PANASONIC_A_TYPE_M
C11: FILTER; C0805
DC/DC_CNVRT: TSR2-2450; TSR2
DC/DC_CONVERTER: UEI15
DVL_OUT: KK254_VERT_2PIN""; KK254_VERT_2PIN
HYP1, HYP2: KK254_10-PIN
I2C: KK254_VERT_2PIN""; KK254_VERT_2PIN
I2C1: KK254_10-PIN
INPT_CRRNT_SNSR: ACS713SOIC; ACS713-SOIC
IO-EXPANDER: PCF8574T; SO16W
MAGREAD: HE151TR-ND
R4, R15, R16, R17: 5k; R0805
RXTX: KK254_10-PIN
U1: BME280; BME280_LGA
U$1: KUHP-5XX1-XX; KUHP_6.35MM-QUICK-CONNECT
U$2, U$4, U$5, U$6: BCS-106-L-D-PE-BE; 4-PIN-BIGPOWER
U$3: TIVA-C_EVAL
UWE_CRRNT_SNSR: ACS713SOIC; ACS713-SOIC
VDIV1(R), VDIV3: 90kO; R0805
VDIV2(R), VDIV4: 10kO; R0805

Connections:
3.3V: I2C1.P$9 (9), R15.1, R16.1, U1.P$2 (!CS), U1.P$5 (SDO/ADR), U1.P$6 (VDDIO), U1.P$8 (VDD), U$3.1-1 (3V3)
5V: 5V_CRRNT_SNSR.P$3 (IP-), 5V_CRRNT_SNSR.P$4 (IP-), 10V_CRRNT_SNSR.P$8 (VCC), A-2-D.10 (REF), A-2-D.16 (VDD), C1.2, C3.2, C7.2, INPT_CRRNT_SNSR.P$8 (VCC), IO-EXPANDER.1 (A0), IO-EXPANDER.16 (VDD), R4.2, R17.2, U$3.3-1 (5V), UWE_CRRNT_SNSR.P$8 (VCC)
5V_CNVTD: 5V_CRRNT_SNSR.P$1 (IP+), 5V_CRRNT_SNSR.P$2 (IP+), 5V_CRRNT_SNSR.P$8 (VCC), C9.2, C11.1, DC/DC_CNVRT.3 (+V_OUT)
5V_CURRENT: 5V_CRRNT_SNSR.P$7 (VIOUT), A-2-D.6 (CH5)
5V_FILT: 5V_CRRNT_SNSR.P$6 (FILTER), C10.2
10V_CURRENT: 10V_CRRNT_SNSR.P$7 (VIOUT), A-2-D.4 (CH3)
10V_EN: 10V_REGULATOR.INHIBIT (!INHIBIT!), IO-EXPANDER.6 (P2)
10V_OUT: 10V_CRRNT_SNSR.P$1 (IP+), 10V_CRRNT_SNSR.P$2 (IP+), 10V_REGULATOR.SENSE (VOSENSE), 10V_REGULATOR.VOUT (VO), C6.+
10V_VOLTAGE: A-2-D.5 (CH4), VDIV3.2, VDIV4.1
+VIN: DC/DC_CONVERTER.+VIN, UWE_CRRNT_SNSR.P$3 (IP-), UWE_CRRNT_SNSR.P$4 (IP-)
BATTERY_LINE: BATTERY_OUT.P$2, U$1.7A (7), U$1.7B (7), U$4.P$1 (1), U$4.P$2 (2), U$4.P$3 (3), U$4.P$4 (4), U$5.P$1 (1), U$5.P$2 (2), U$5.P$3 (3)
CS_0: U$3.2-9 (PA3)
CS_2: U$3.1-2 (PB5)
DGND: I2C1.P$10 (10), U1.P$1 (GND1), U1.P$7 (GND2)
FILTER: C4.2, UWE_CRRNT_SNSR.P$6 (FILTER)
FLTR_10V: 10V_CRRNT_SNSR.P$6 (FILTER), C8.2
GND: 5V_CRRNT_SNSR.P$5 (GND), 10V_CRRNT_SNSR.P$5 (GND), 10V_OUT.P$1, 10V_REGULATOR.GND1, 10V_REGULATOR.GND2, A-2-D.9 (GND), A-2-D.12 (A0), A-2-D.13 (A1), ADJUST(R).2, BATTERY_INPUT.P$1, BATTERY_OUT.P$1, C1.1, C2.1, C3.1, C4.1, C5.-, C6.-, C7.1, C8.1, C9.1, C10.1, C11.2, DC/DC_CNVRT.2 (GND), DC/DC_CONVERTER.-VIN, INPT_CRRNT_SNSR.P$5 (GND), IO-EXPANDER.2 (A1), IO-EXPANDER.3 (A2), IO-EXPANDER.8 (VSS), U$1.5A (5), U$1.5B (5), U$1.AA (A), U$1.AB (A), U$2.P$1 (1), U$2.P$2 (2), U$2.P$3 (3), U$2.P$4 (4), U$3.2-1 (GND), U$3.3-2 (GND), U$6.P$1 (1), U$6.P$2 (2), U$6.P$3 (3), U$6.P$4 (4), UWE_CRRNT_SNSR.P$5 (GND), VDIV2(R).2, VDIV4.2
INPT_FILT: C2.2, INPT_CRRNT_SNSR.P$6 (FILTER)
INPUT_CURRENT: A-2-D.1 (CH0), INPT_CRRNT_SNSR.P$7 (VIOUT)
INPUT_VOLTAGE: A-2-D.2 (CH1), VDIV1(R).2, VDIV2(R).1
MISO_0: RXTX.P$4 (4), U$3.2-8 (PA4)
MISO_3: U$3.3-5 (PD2)
MOSI_0: RXTX.P$3 (3), U$3.1-8 (PA5)
MOSI_3: U$3.3-6 (PD3)
unnamed: 10V_REGULATOR.ADJUST (VOADJUST), ADJUST(R).1
PE2: U$3.3-8 (PE2)
PE3: U$3.3-9 (PE3)
PROCESSED_10V_OUT: 10V_CRRNT_SNSR.P$3 (IP-), 10V_CRRNT_SNSR.P$4 (IP-), 10V_OUT.P$2, MAGREAD.P$1, VDIV3.1
PROCESSED_UEI_OUTPUT: DC/DC_CONVERTER.+VOUT, DVL_OUT.P$2
PROC_INPUT: 10V_REGULATOR.VIN (VI), C5.+, DC/DC_CNVRT.1 (+V_IN), INPT_CRRNT_SNSR.P$3 (IP-), INPT_CRRNT_SNSR.P$4 (IP-), U$1.2A (2), U$1.2B (2), UWE_CRRNT_SNSR.P$1 (IP+), UWE_CRRNT_SNSR.P$2 (IP+), VDIV1(R).1
PUSH1: U$3.4-10 (PF4)
PWM0: HYP1.P$3 (3), U$3.2-7 (PD0)
PWM1: HYP1.P$4 (4), U$3.2-6 (PD1)
PWM2: HYP1.P$5 (5), U$3.1-5 (PE4)
PWM3: HYP1.P$6 (6), U$3.1-6 (PE5)
PWM4: HYP1.P$7 (7), U$3.2-4 (PF0)
PWM5: HYP1.P$8 (8), U$3.3-10 (PF1)
PWM6: HYP1.P$9 (9), U$3.4-1 (PF2)
PWM7: HYP1.P$10 (10), U$3.4-2 (PF3)
RES: U$3.2-5 (!RESET!)
RLY_10V: MAGREAD.P$2, U$1.BA (B), U$1.BB (B)
RX_CF: U$3.2-3 (PE0)
RX_MC: RXTX.P$8 (8), U$3.4-4 (PC4)
RX_MD: RXTX.P$6 (6), U$3.4-8 (PD6)
RX_MF: U$3.1-3 (PB0)
RX_SF: RXTX.P$9 (9), U$3.4-6 (PC6)
SCK_0: U$3.2-10 (PA2)
SCL: A-2-D.14 (SCL), I2C.P$2, IO-EXPANDER.14 (SCL)
SCL_0: I2C1.P$5 (5), R4.1, U$3.2-2 (PB2)
SCL_1: I2C1.P$7 (7), R15.2, U1.P$4 (SCK/SCL), U$3.1-9 (PA6)
SDA: A-2-D.15 (SDA), I2C.P$1, IO-EXPANDER.15 (SDA)
SDA_0: I2C1.P$6 (6), R17.1, U$3.4-3 (PB3)
SDA_1: I2C1.P$8 (8), R16.2, U1.P$3 (SDI/SDA), U$3.1-10 (PA7)
SPI_CLK_2: U$3.1-7 (PB4)
TX_CF: U$3.3-7 (PE1)
TX_MC: RXTX.P$7 (7), U$3.4-5 (PC5)
TX_MD: RXTX.P$5 (5), U$3.4-9 (PD7)
TX_MF: U$3.1-4 (PB1)
TX_SF: RXTX.P$10 (10), U$3.4-7 (PC7)
UEI_EN: DC/DC_CONVERTER.ON/OFFCNTRL (ON/OFF), IO-EXPANDER.4 (P0)
UEI_GND: DC/DC_CONVERTER.-VOUT, DVL_OUT.P$1
UWE_CURRENT: A-2-D.3 (CH2), UWE_CRRNT_SNSR.P$7 (VIOUT)
VBAT: 20A_FUSE.P$1, 20A_FUSE.P$2, BATTERY_INPUT.P$2
VBAT_P: 20A_FUSE.P$3, 20A_FUSE.P$4, INPT_CRRNT_SNSR.P$1 (IP+), INPT_CRRNT_SNSR.P$2 (IP+)

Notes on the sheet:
MAG_READ
Ribbon Cables Leading to Other Boards
BME Device

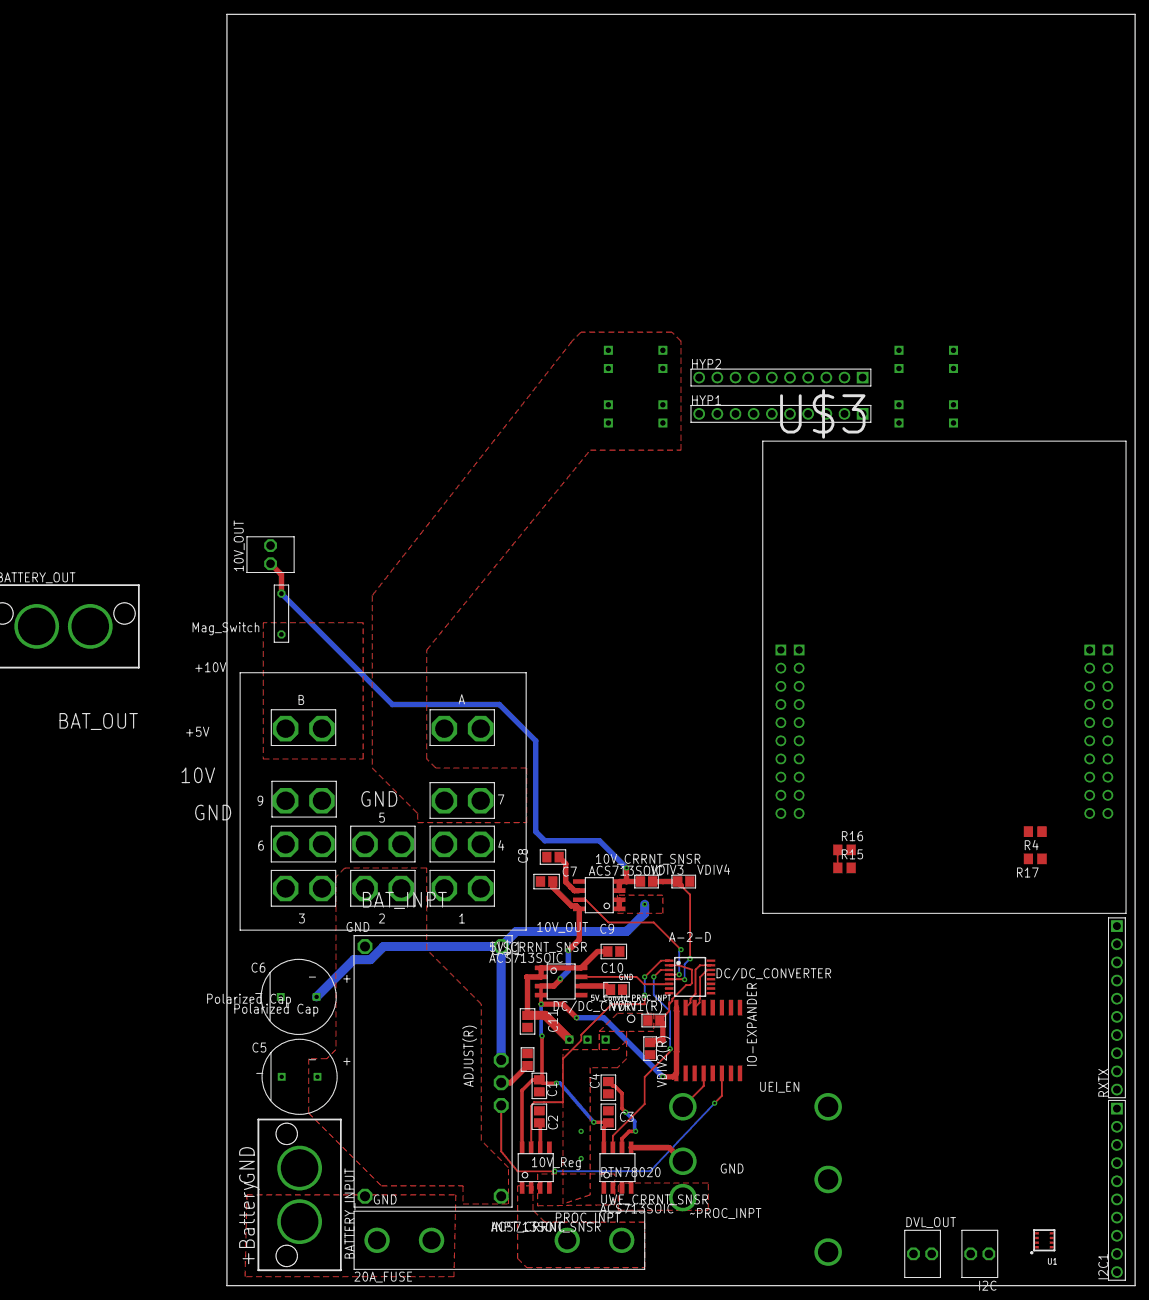
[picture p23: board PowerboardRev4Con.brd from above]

Board: 2 copper layers, 127.0 x 177.8 mm, 47 parts (0 on the bottom side), 50 nets.

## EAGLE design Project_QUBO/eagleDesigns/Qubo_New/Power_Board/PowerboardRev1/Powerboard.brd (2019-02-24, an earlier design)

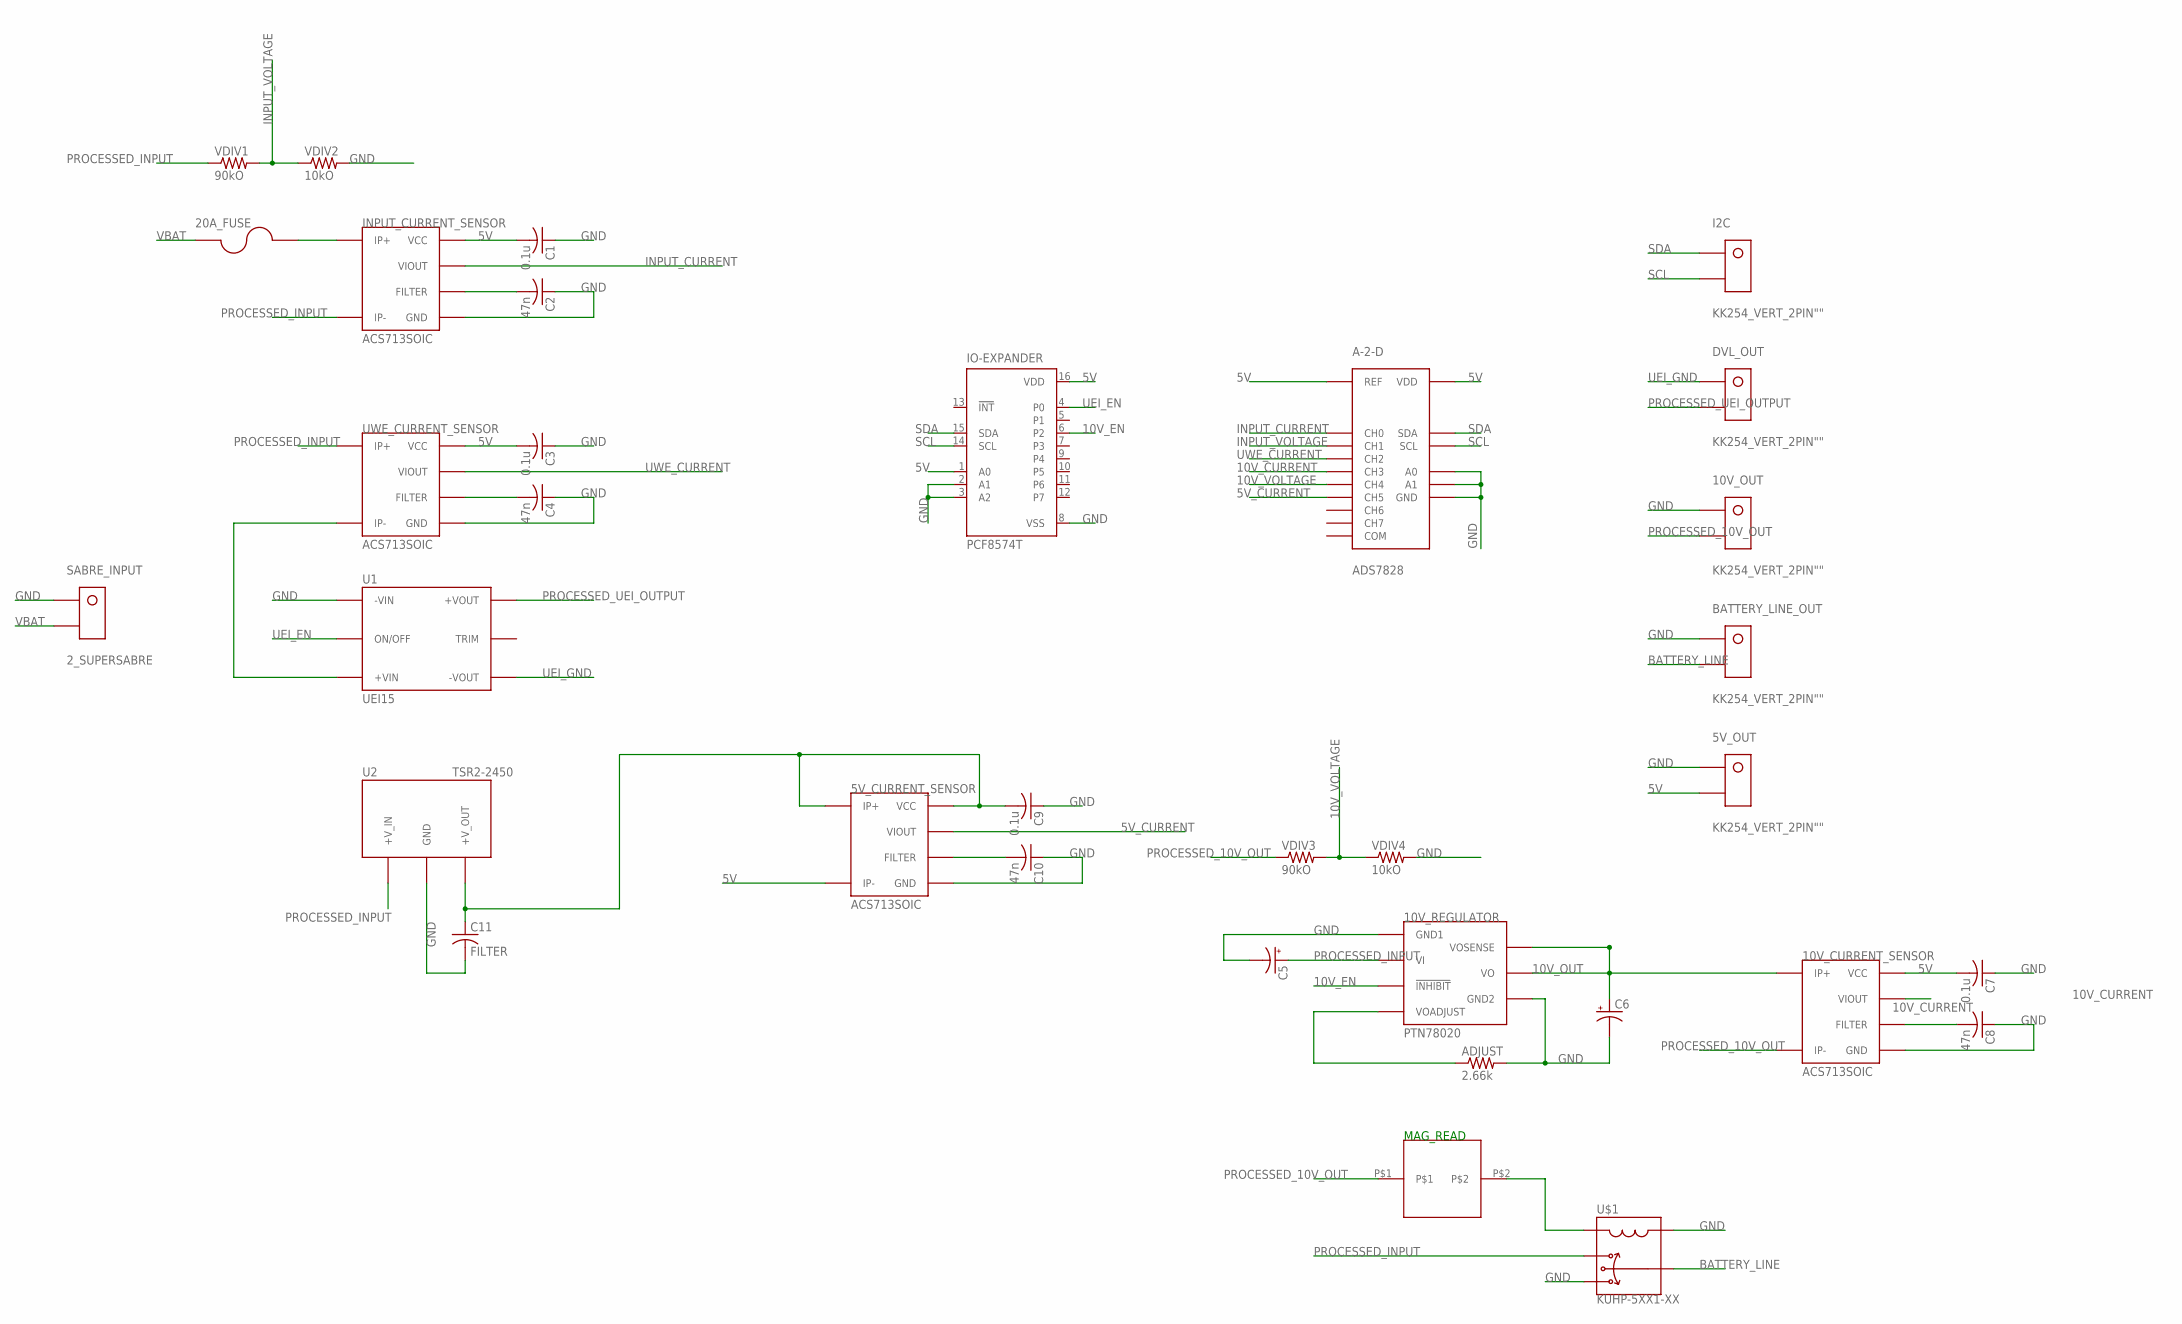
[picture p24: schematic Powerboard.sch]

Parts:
5V_CURRENT_SENSOR, 10V_CURRENT_SENSOR: ACS713SOIC; ACS713-SOIC
5V_OUT, 10V_OUT: KK254_VERT_2PIN""; KK254_VERT_2PIN
10V_REGULATOR: PTN78020; PTN
20A_FUSE: BOWED-1.25"-FUSECLIPS; 1.25"_FUSECLIPS
A-2-D: ADS7828; TSSOP16
ADJUST: 2.66k; R0805
BATTERY_LINE_OUT: KK254_VERT_2PIN""; KK254_VERT_2PIN
C1, C3, C7, C9: 0.1u; C0805
C2, C4, C8, C10: 47n; C0805
C5, C6: CPOL-US; PANASONIC_A_TYPE_M
C11: FILTER; C0805
DVL_OUT: KK254_VERT_2PIN""; KK254_VERT_2PIN
I2C: KK254_VERT_2PIN""; KK254_VERT_2PIN
INPUT_CURRENT_SENSOR: ACS713SOIC; ACS713-SOIC
IO-EXPANDER: PCF8574T; SO16W
MAGREAD: HE151TR-ND
SABRE_INPUT: 2_SUPERSABRE; SUPERSABRE_2CIRCUIT
U1: UEI15
U2: TSR2-2450; TSR2
U$1: KUHP-5XX1-XX; KUHP_6.35MM-QUICK-CONNECT
UWE_CURRENT_SENSOR: ACS713SOIC; ACS713-SOIC
VDIV1, VDIV3: 90kO; R0805
VDIV2, VDIV4: 10kO; R0805

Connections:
5V: 5V_CURRENT_SENSOR.P$3 (IP-), 5V_CURRENT_SENSOR.P$4 (IP-), 5V_OUT.P$2, 10V_CURRENT_SENSOR.P$8 (VCC), A-2-D.10 (REF), A-2-D.16 (VDD), C1.2, C3.2, C7.2, INPUT_CURRENT_SENSOR.P$8 (VCC), IO-EXPANDER.1 (A0), IO-EXPANDER.16 (VDD), UWE_CURRENT_SENSOR.P$8 (VCC)
5V_CURRENT: 5V_CURRENT_SENSOR.P$7 (VIOUT), A-2-D.6 (CH5)
10V_CURRENT: 10V_CURRENT_SENSOR.P$7 (VIOUT), A-2-D.4 (CH3)
10V_EN: 10V_REGULATOR.INHIBIT (!INHIBIT!), IO-EXPANDER.6 (P2)
10V_OUT: 10V_CURRENT_SENSOR.P$1 (IP+), 10V_CURRENT_SENSOR.P$2 (IP+), 10V_REGULATOR.SENSE (VOSENSE), 10V_REGULATOR.VOUT (VO), C6.+
10V_VOLTAGE: A-2-D.5 (CH4), VDIV3.2, VDIV4.1
BATTERY_LINE: BATTERY_LINE_OUT.P$2, U$1.7A (7), U$1.7B (7)
GND: 5V_CURRENT_SENSOR.P$5 (GND), 5V_OUT.P$1, 10V_CURRENT_SENSOR.P$5 (GND), 10V_OUT.P$1, 10V_REGULATOR.GND1, 10V_REGULATOR.GND2, A-2-D.9 (GND), A-2-D.12 (A0), A-2-D.13 (A1), ADJUST.2, BATTERY_LINE_OUT.P$1, C1.1, C2.1, C3.1, C4.1, C5.-, C6.-, C7.1, C8.1, C9.1, C10.1, C11.2, INPUT_CURRENT_SENSOR.P$5 (GND), IO-EXPANDER.2 (A1), IO-EXPANDER.3 (A2), IO-EXPANDER.8 (VSS), SABRE_INPUT.P$1, U1.-VIN, U2.2 (GND), U$1.5A (5), U$1.5B (5), U$1.AA (A), U$1.AB (A), UWE_CURRENT_SENSOR.P$5 (GND), VDIV2.2, VDIV4.2
INPUT_CURRENT: A-2-D.1 (CH0), INPUT_CURRENT_SENSOR.P$7 (VIOUT)
INPUT_VOLTAGE: A-2-D.2 (CH1), VDIV1.2, VDIV2.1
unnamed: 20A_FUSE.P$3, 20A_FUSE.P$4, INPUT_CURRENT_SENSOR.P$1 (IP+), INPUT_CURRENT_SENSOR.P$2 (IP+)
unnamed: C2.2, INPUT_CURRENT_SENSOR.P$6 (FILTER)
unnamed: 5V_CURRENT_SENSOR.P$6 (FILTER), C10.2
unnamed: 5V_CURRENT_SENSOR.P$1 (IP+), 5V_CURRENT_SENSOR.P$2 (IP+), 5V_CURRENT_SENSOR.P$8 (VCC), C9.2, C11.1, U2.3 (+V_OUT)
unnamed: 10V_REGULATOR.ADJUST (VOADJUST), ADJUST.1
unnamed: U1.+VIN, UWE_CURRENT_SENSOR.P$3 (IP-), UWE_CURRENT_SENSOR.P$4 (IP-)
unnamed: C4.2, UWE_CURRENT_SENSOR.P$6 (FILTER)
unnamed: MAGREAD.P$2, U$1.BA (B), U$1.BB (B)
unnamed: 10V_CURRENT_SENSOR.P$6 (FILTER), C8.2
PROCESSED_10V_OUT: 10V_CURRENT_SENSOR.P$3 (IP-), 10V_CURRENT_SENSOR.P$4 (IP-), 10V_OUT.P$2, MAGREAD.P$1, VDIV3.1
PROCESSED_INPUT: 10V_REGULATOR.VIN (VI), C5.+, INPUT_CURRENT_SENSOR.P$3 (IP-), INPUT_CURRENT_SENSOR.P$4 (IP-), U2.1 (+V_IN), U$1.2A (2), U$1.2B (2), UWE_CURRENT_SENSOR.P$1 (IP+), UWE_CURRENT_SENSOR.P$2 (IP+), VDIV1.1
PROCESSED_UEI_OUTPUT: DVL_OUT.P$2, U1.+VOUT
SCL: A-2-D.14 (SCL), I2C.P$2, IO-EXPANDER.14 (SCL)
SDA: A-2-D.15 (SDA), I2C.P$1, IO-EXPANDER.15 (SDA)
UEI_EN: IO-EXPANDER.4 (P0), U1.ON/OFFCNTRL (ON/OFF)
UEI_GND: DVL_OUT.P$1, U1.-VOUT
UWE_CURRENT: A-2-D.3 (CH2), UWE_CURRENT_SENSOR.P$7 (VIOUT)
VBAT: 20A_FUSE.P$1, 20A_FUSE.P$2, SABRE_INPUT.P$2

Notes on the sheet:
MAG_READ

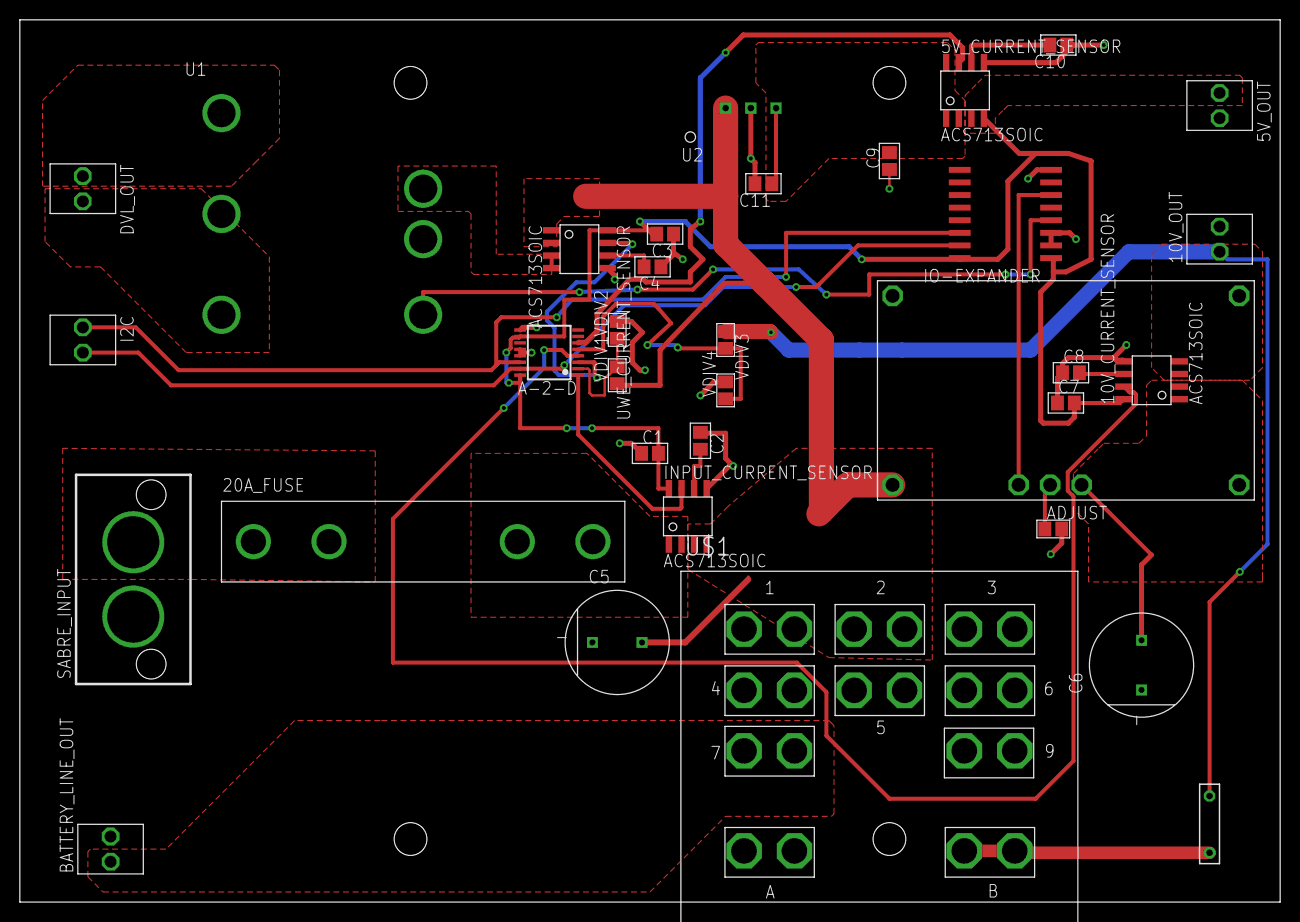
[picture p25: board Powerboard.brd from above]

Board: 2 copper layers, 127.0 x 88.9 mm, 34 parts (0 on the bottom side), 28 nets.

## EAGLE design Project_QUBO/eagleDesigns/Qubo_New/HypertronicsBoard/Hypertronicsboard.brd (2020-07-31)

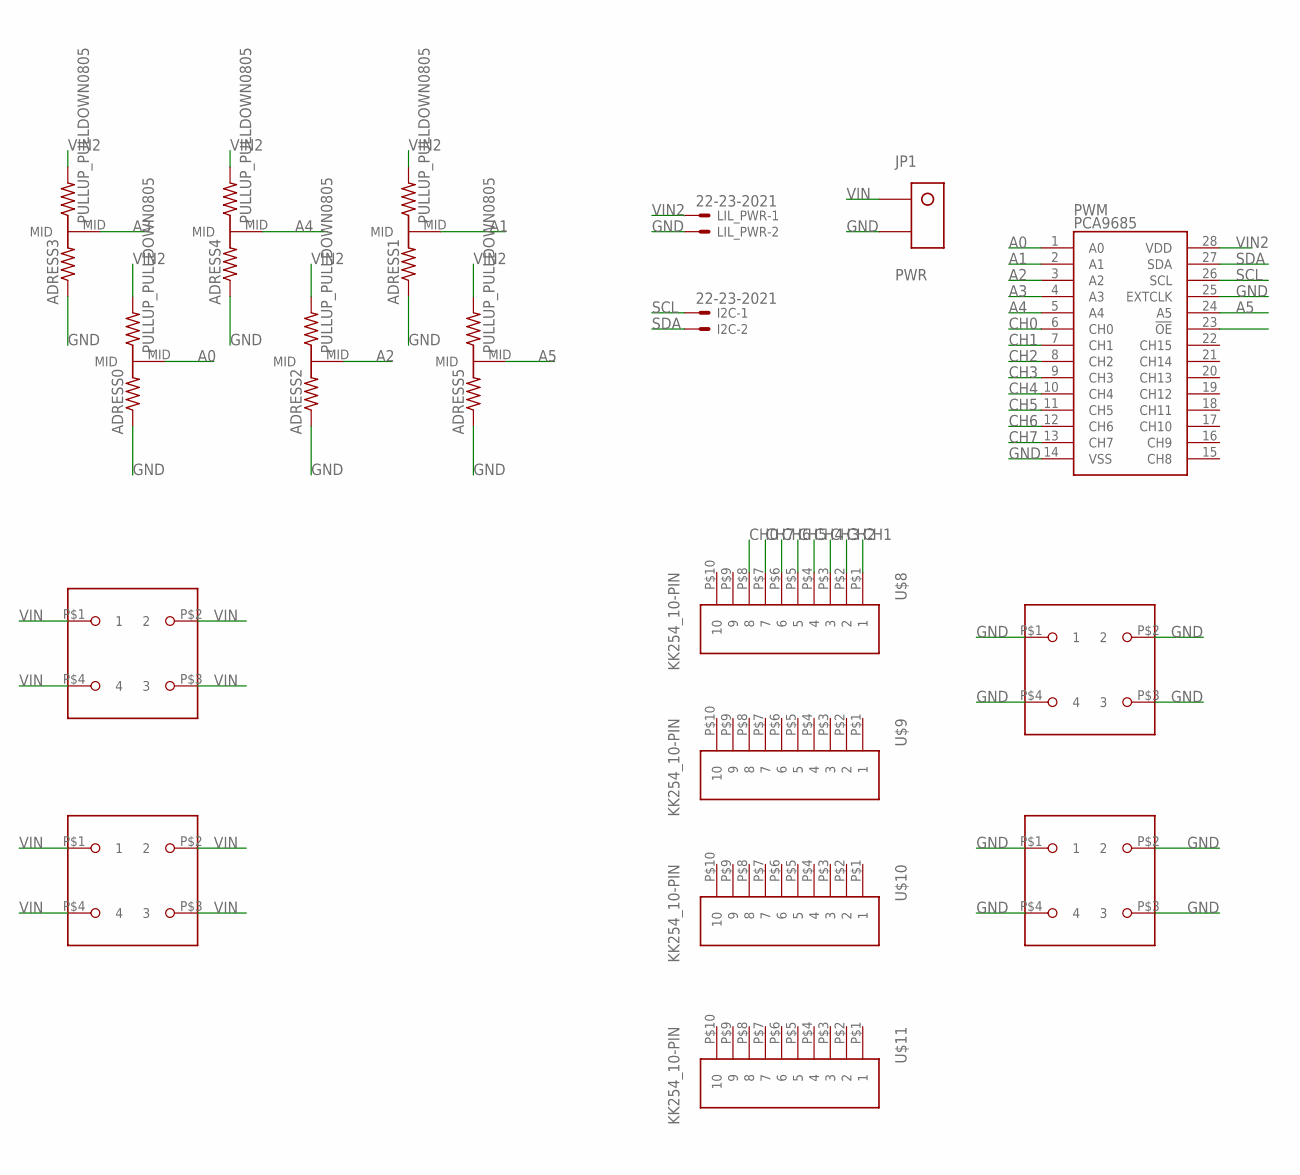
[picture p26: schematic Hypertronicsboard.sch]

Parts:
ADRESS0, ADRESS1, ADRESS2, ADRESS3, ADRESS4, ADRESS5: PULLUP_PULLDOWN0805; PULLUP_PULLDOWN_0805
I2C: 22-23-2021
JP1: PWR; SUPERSABRE_2CIRCUIT
LIL_PWR: 22-23-2021
PWM: PCA9685; TSSOP-28_4MM
U$1, U$2, U$3, U$4: BCS-106-L-D-PE-BE; 4-PIN-BIGPOWER
U$8, U$9, U$10, U$11: KK254_10-PIN

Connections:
A0: ADRESS0.MID, PWM.1 (A0)
A1: ADRESS1.MID, PWM.2 (A1)
A2: ADRESS2.MID, PWM.3 (A2)
A3: ADRESS3.MID, PWM.4 (A3)
A4: ADRESS4.MID, PWM.5 (A4)
A5: ADRESS5.MID, PWM.24 (A5)
CH0: PWM.6 (CH0), U$8.P$8 (8)
CH1: PWM.7 (CH1), U$8.P$1 (1)
CH2: PWM.8 (CH2), U$8.P$2 (2)
CH3: PWM.9 (CH3), U$8.P$3 (3)
CH4: PWM.10 (CH4), U$8.P$4 (4)
CH5: PWM.11 (CH5), U$8.P$5 (5)
CH6: PWM.12 (CH6), U$8.P$6 (6)
CH7: PWM.13 (CH7), U$8.P$7 (7)
GND: ADRESS0.GND, ADRESS1.GND, ADRESS2.GND, ADRESS3.GND, ADRESS4.GND, ADRESS5.GND, JP1.P$2, LIL_PWR.2, PWM.14 (VSS), PWM.25 (EXTCLK), U$3.P$1 (1), U$3.P$2 (2), U$3.P$3 (3), U$3.P$4 (4), U$4.P$1 (1), U$4.P$2 (2), U$4.P$3 (3), U$4.P$4 (4)
SCL: I2C.1, PWM.26 (SCL)
SDA: I2C.2, PWM.27 (SDA)
VIN: JP1.P$1, U$1.P$1 (1), U$1.P$2 (2), U$1.P$3 (3), U$1.P$4 (4), U$2.P$1 (1), U$2.P$2 (2), U$2.P$3 (3), U$2.P$4 (4)
VIN2: ADRESS0.VCC (PWR), ADRESS1.VCC (PWR), ADRESS2.VCC (PWR), ADRESS3.VCC (PWR), ADRESS4.VCC (PWR), ADRESS5.VCC (PWR), LIL_PWR.1, PWM.28 (VDD)

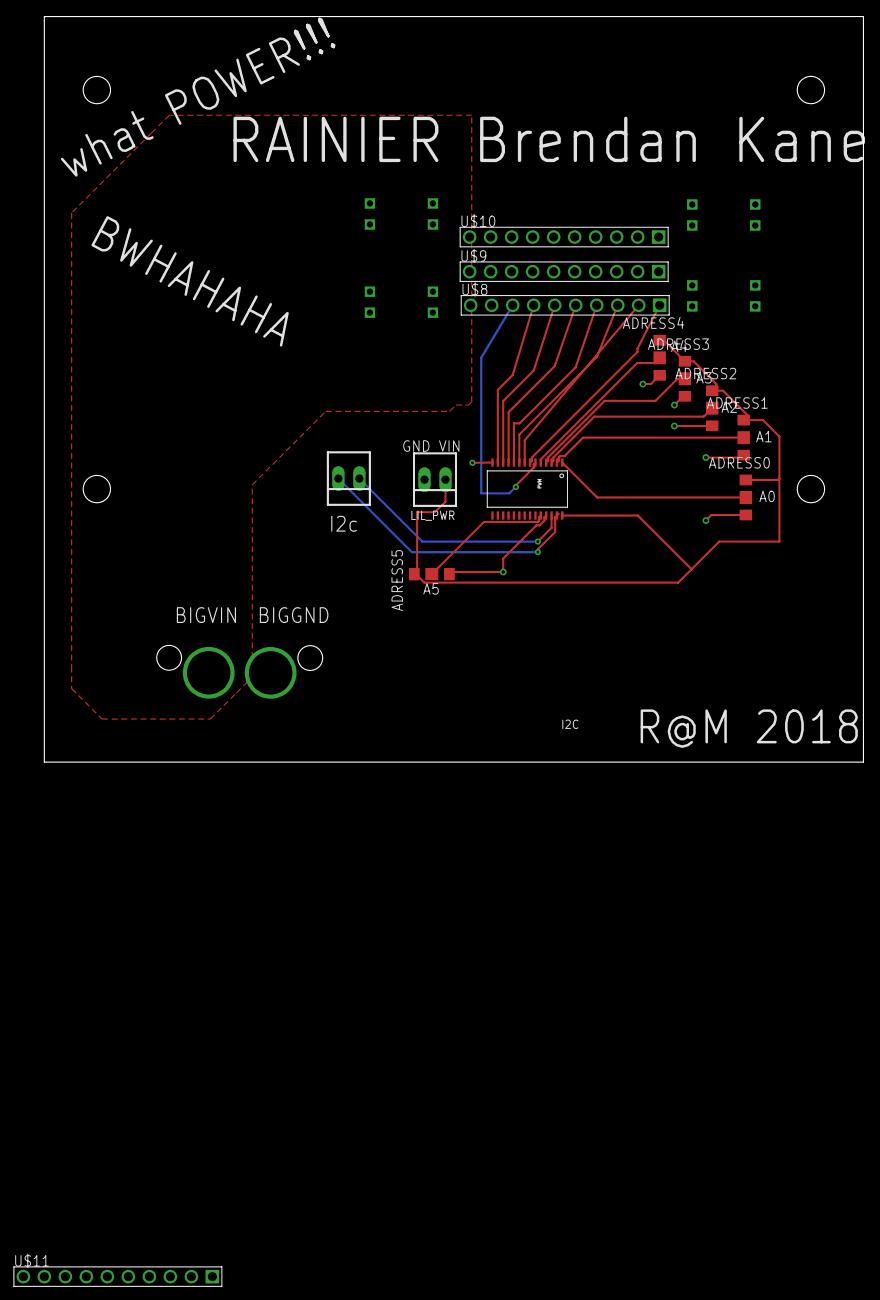
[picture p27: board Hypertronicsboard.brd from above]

Board: 2 copper layers, 99.1 x 90.2 mm, 18 parts (1 on the bottom side), 19 nets.

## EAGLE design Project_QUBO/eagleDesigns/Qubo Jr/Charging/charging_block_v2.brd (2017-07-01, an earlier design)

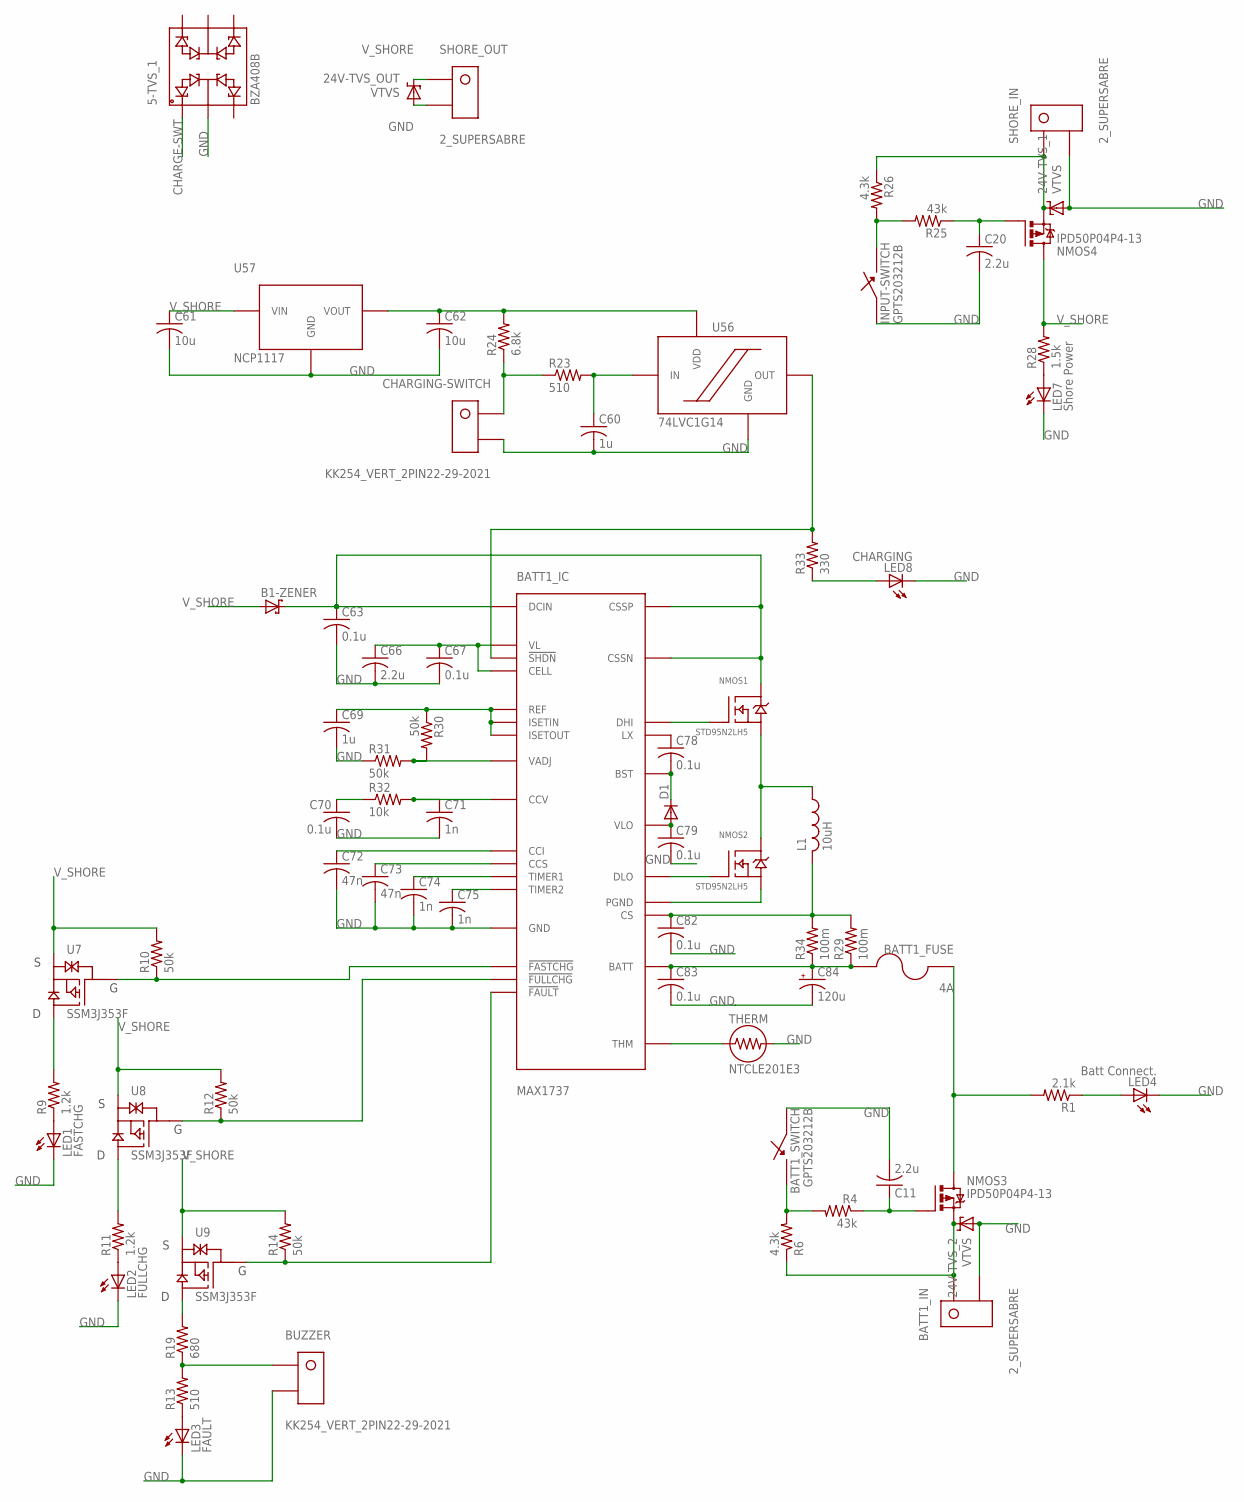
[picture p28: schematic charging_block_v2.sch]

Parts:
5-TVS_1: BZA408B; SOT457
24V-TVS_1, 24V-TVS_2, 24V-TVS_OUT: VTVS; DO-219AB
B1-ZENER: SCHOTTKY-DIODESOD-106; SOD106-R
BATT1_FUSE: 4A; 154-OMNI-BLOK
BATT1_IC: MAX1737; QSOP28
BATT1_IN: 2_SUPERSABRE; SUPERSABRE_2CIRCUIT
BATT1_SWITCH: GPTS203212B; GPTS203211B
BUZZER: KK254_VERT_2PIN22-29-2021; KK254_VERT_2PIN
C11, C20, C66: 2.2u; C0805
C60, C69: 1u; C0805
C61, C62: 10u; C0805
C63, C67, C70, C78, C79, C82, C83: 0.1u; C0805
C71, C74, C75: 1n; C0805
C72, C73: 47n; C0805
C84: 120u; E3,5-8
CHARGING-SWITCH: KK254_VERT_2PIN22-29-2021; KK254_VERT_2PIN
D1: DIODE-SOD123; SOD123
INPUT-SWITCH: GPTS203212B; GPTS203211B
L1: 10uH; L6100
LED1: FASTCHG; CHIP-LED0805
LED2: FULLCHG; CHIP-LED0805
LED3: FAULT; CHIP-LED0805
LED4: Batt Connect.; CHIP-LED0805
LED7: Shore Power; CHIP-LED0805
LED8: CHARGING; CHIP-LED0805
NMOS1, NMOS2: STD95N2LH5; DPAK
NMOS3, NMOS4: IPD50P04P4-13; TO252-3
R1: 2.1k; R0805
R4, R25: 43k; R0805
R6, R26: 4.3k; R0805
R9, R11: 1.2k; R0805
R10, R12, R14, R30, R31: 50k; R0805
R13, R23: 510; R0805
R19: 680; R0805
R24: 6.8k; R0805
R28: 1.5k; R0805
R29, R34: 100m; R2512
R32: 10k; R0805
R33: 330; R0805
SHORE_IN: 2_SUPERSABRE; SUPERSABRE_2CIRCUIT
SHORE_OUT: 2_SUPERSABRE; SUPERSABRE_2CIRCUIT
THERM: NTCLE201E3; 2-0.3MM-LEADS
U7, U8, U9: SSM3J353F; SOT-346-3/S-MINI
U56: 74LVC1G14; TSSOP5
U57: NCP1117; SOT-223

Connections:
!FASTCHG!_1: BATT1_IC.16 (!FASTCHG!), R10.1, U7.P$1 (G)
!FAULT!_1: BATT1_IC.15 (!FAULT!), R14.1, U9.P$1 (G)
!FULLCHG!_1: BATT1_IC.17 (!FULLCHG!), R12.1, U8.P$1 (G)
!SHDN!_1: BATT1_IC.18 (!SHDN!), R33.2, U56.P$4 (OUT)
BATT1_P: 24V-TVS_2.P$2 (C), BATT1_IN.P$1, NMOS3.TAB (D), R6.1
BATT_1: BATT1_FUSE.P$2, BATT1_IC.7 (BATT), C83.1, C84.+, R29.1, R34.1
CCI_1: BATT1_IC.11 (CCI), C72.1
CCS_1: BATT1_IC.10 (CCS), C73.1
CCV_1: BATT1_IC.9 (CCV), C71.1, R32.2
CHARGE-SWT: 5-TVS_1.P$1, CHARGING-SWITCH.P$1, R23.1, R24.1
CHG-OUT_1: BATT1_FUSE.P$1, NMOS3.3 (S), R1.2
DCIN_1: B1-ZENER.C, BATT1_IC.26 (CSSN), BATT1_IC.27 (CSSP), BATT1_IC.28 (DCIN), C63.1, NMOS1.TAB (D)
DHI1: BATT1_IC.25 (DHI), NMOS1.1 (G)
DLO1: BATT1_IC.21 (DLO), NMOS2.1 (G)
FET-G_1: C11.1, NMOS3.1 (G), R4.1
GND: 5-TVS_1.P$2, 24V-TVS_1.P$1 (A), 24V-TVS_2.P$1 (A), 24V-TVS_OUT.P$1 (A), BATT1_IC.6 (GND), BATT1_IN.P$2, BATT1_SWITCH.P$1, BUZZER.P$2, C11.2, C20.2, C60.2, C61.2, C62.2, C63.2, C66.2, C67.2, C69.2, C70.2, C71.2, C72.2, C73.2, C74.2, C75.2, C79.2, C82.2, C83.2, C84.-, CHARGING-SWITCH.P$2, INPUT-SWITCH.P$1, LED1.C, LED2.C, LED3.C, LED4.C, LED7.C, LED8.C, R31.1, SHORE_IN.P$2, SHORE_OUT.P$2, THERM.P$2 (2), U56.P$3 (GND), U57.P$1 (GND)
LIN_1: L1.P$1 (1), NMOS1.3 (S), NMOS2.TAB (D)
LOUT_1: BATT1_IC.19 (CS), C82.1, L1.P$2 (2), R29.2, R34.2
unnamed: LED4.A, R1.1
unnamed: LED1.A, R9.1
unnamed: BATT1_IC.20 (PGND), NMOS2.3 (S)
unnamed: LED3.A, R13.1
unnamed: LED2.A, R11.1
unnamed: R9.2, U7.P$2 (D)
unnamed: R11.2, U8.P$2 (D)
unnamed: BUZZER.P$1, R13.2, R19.1
unnamed: R19.2, U9.P$2 (D)
unnamed: LED7.A, R28.1
unnamed: C20.1, NMOS4.1 (G), R25.1
unnamed: C60.1, R23.2, U56.P$2 (IN)
unnamed: INPUT-SWITCH.P$2, R25.2, R26.2
unnamed: BATT1_SWITCH.P$2, R4.2, R6.2
unnamed: C62.1, R24.2, U56.P$5 (VDD), U57.P$2 (VOUT), U57.P$4 (VOUT)
unnamed: LED8.A, R33.1
unnamed: C70.1, R32.1
unnamed: BATT1_IC.24 (LX), C78.1
unnamed: BATT1_IC.23 (BST), C78.2, D1.C
unnamed: BATT1_IC.22 (VLO), C79.1, D1.A
REF_1: BATT1_IC.2 (ISETIN), BATT1_IC.3 (ISETOUT), BATT1_IC.5 (REF), C69.1, R30.1
THM1: BATT1_IC.4 (THM), THERM.P$1 (1)
TIMER1_1: BATT1_IC.13 (TIMER1), C74.1
TIMER2_1: BATT1_IC.14 (TIMER2), C75.1
VADJ_1: BATT1_IC.8 (VADJ), R30.2, R31.2
VIN: 24V-TVS_1.P$2 (C), NMOS4.TAB (D), R26.1, SHORE_IN.P$1
VL_1: BATT1_IC.1 (VL), BATT1_IC.12 (CELL), C66.1, C67.1
V_SHORE: 24V-TVS_OUT.P$2 (C), B1-ZENER.A, C61.1, NMOS4.3 (S), R10.2, R12.2, R14.2, R28.2, SHORE_OUT.P$1, U7.P$3 (S), U8.P$3 (S), U9.P$3 (S), U57.P$3 (VIN)

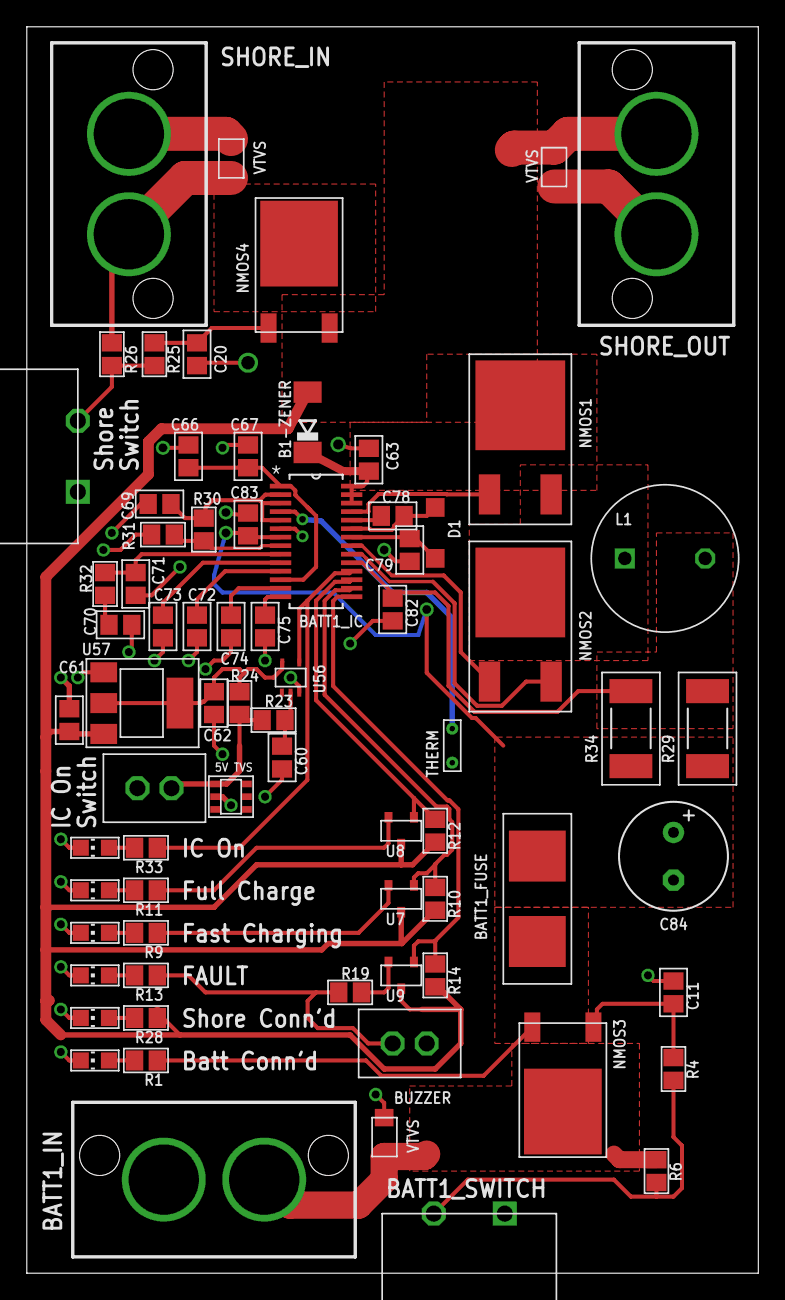
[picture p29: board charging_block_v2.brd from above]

Board: 2 copper layers, 54.6 x 93.0 mm, 73 parts (0 on the bottom side), 46 nets.

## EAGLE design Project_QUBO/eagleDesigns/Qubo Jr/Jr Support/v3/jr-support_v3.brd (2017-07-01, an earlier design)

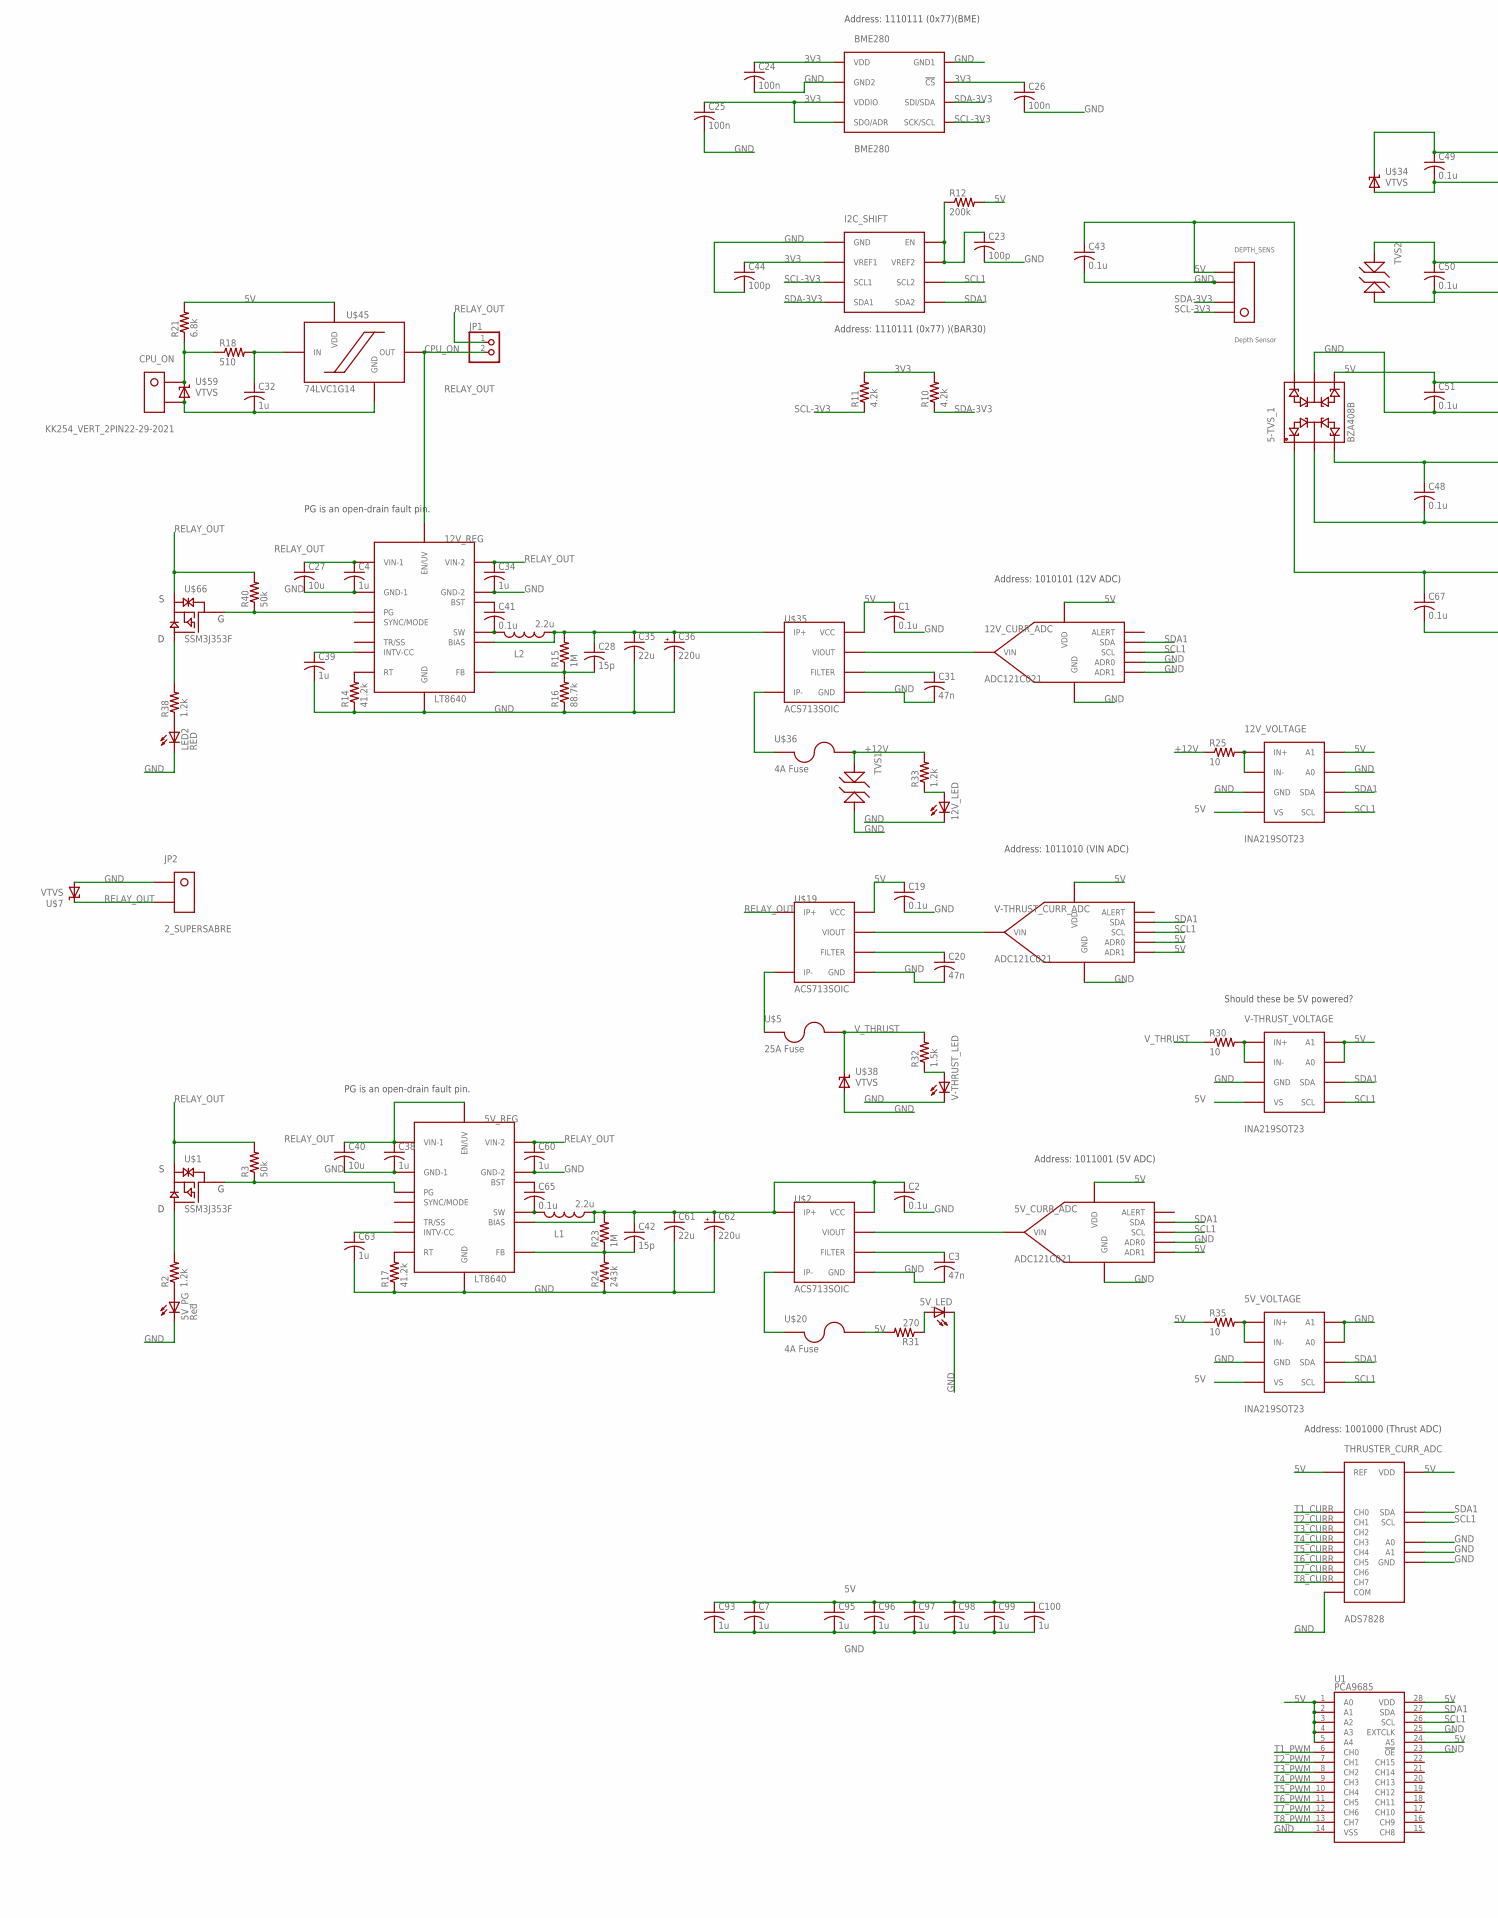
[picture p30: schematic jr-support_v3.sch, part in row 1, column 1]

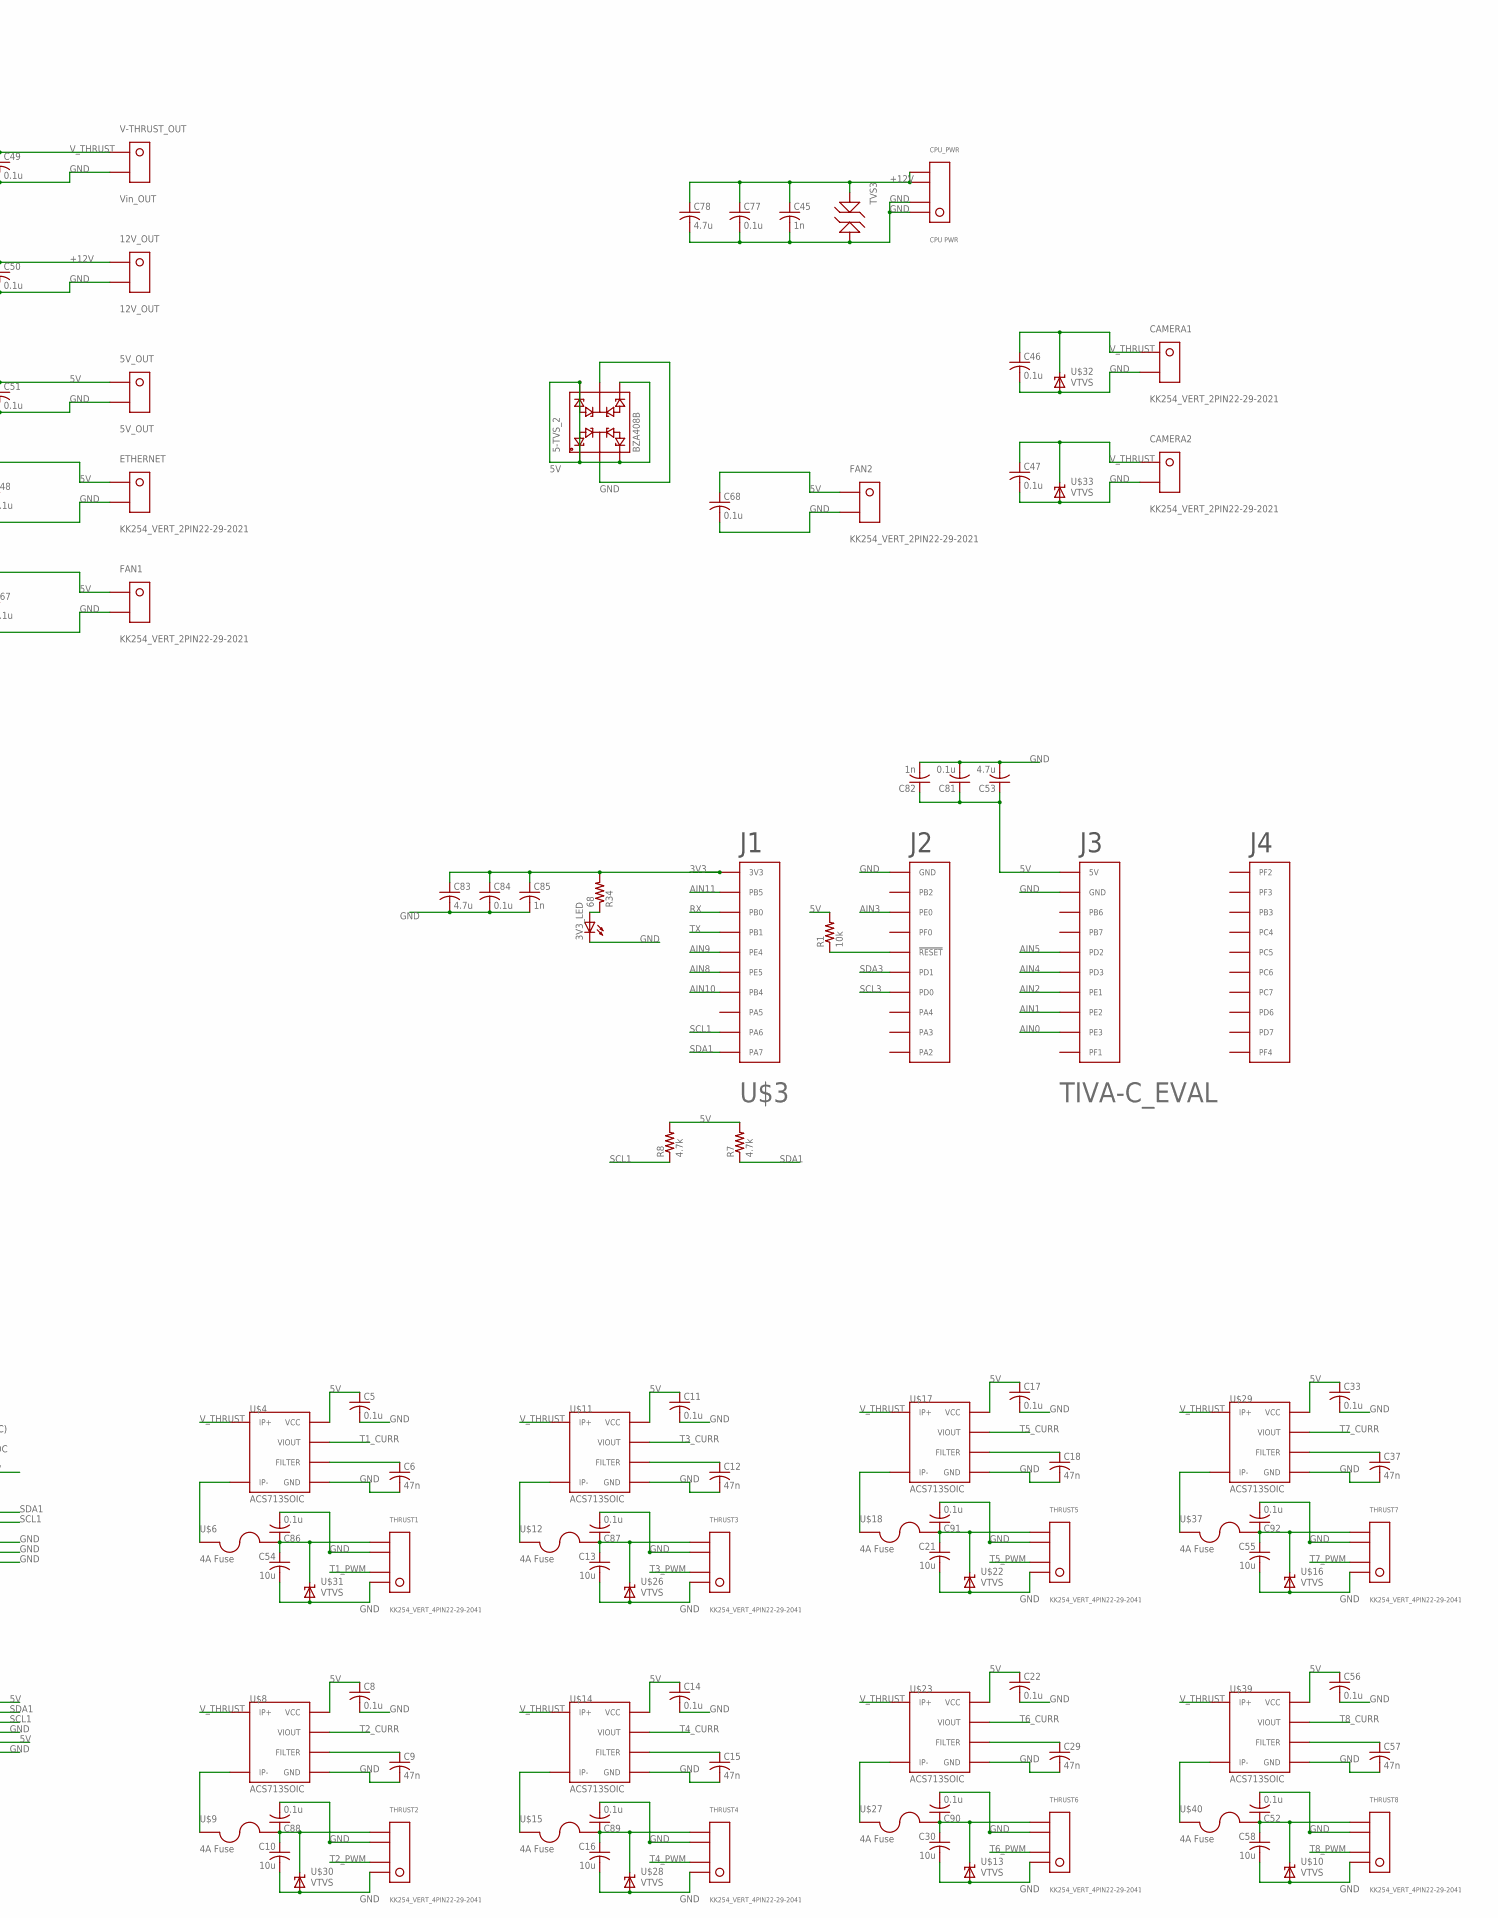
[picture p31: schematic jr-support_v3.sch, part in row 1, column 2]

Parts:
3V3_LED, 5V_LED, 12V_LED: 0805_LED; 0805
5-TVS_1, 5-TVS_2: BZA408B; SOT457
5V_CURR_ADC, 12V_CURR_ADC: ADC121C021; VSSOP-8
5V_OUT: 5V_OUT; KK254_VERT_2PIN
5V_PG: Red; CHIP-LED0805
5V_REG, 12V_REG: LT8640; QFN18-3X4
5V_VOLTAGE, 12V_VOLTAGE: INA219SOT23; SOT-23-8
12V_OUT: 12V_OUT; KK254_VERT_2PIN
BME280: BME280; BME280_LGA
C1, C2, C5, C8, C11, C14, C17, C19, C22, C33, C41, C43, C46, C47, C48, C49, C50, C51, C52, C56, C65, C67, C68, C77, C81, C84, C86, C87, C88, C89, C90, C91, C92: 0.1u; C0805
C3, C6, C9, C12, C15, C18, C20, C29, C31, C37, C57: 47n; C0805
C4, C7, C32, C34, C38, C39, C60, C63, C93, C95, C96, C97, C98, C99, C100: 1u; C0805
C10, C13, C16, C21, C27, C30, C40, C54, C55, C58: 10u; C0805
C23, C44: 100p; C0805
C24, C25, C26: 100n; C0805
C28, C42: 15p; C0805
C35, C61: 22u; C0805
C36, C62: 220u; C-F80
C45, C82, C85: 1n; C0805
C53, C78, C83: 4.7u; C0805
CAMERA1, CAMERA2: KK254_VERT_2PIN22-29-2021; KK254_VERT_2PIN
CPU_ON: KK254_VERT_2PIN22-29-2021; KK254_VERT_2PIN
CPU_PWR: CPU PWR; KK254_VERT_4PIN
DEPTH_SENS: Depth Sensor; KK254_VERT_4PIN
ETHERNET: KK254_VERT_2PIN22-29-2021; KK254_VERT_2PIN
FAN1, FAN2: KK254_VERT_2PIN22-29-2021; KK254_VERT_2PIN
I2C_SHIFT: PCA9306DCT; SM8
JP1: PINHD-1X2; 1X02
JP2: 2_SUPERSABRE; SUPERSABRE_2CIRCUIT
L1, L2: 2.2u; L0740
LED2: RED; CHIP-LED0805
R1: 10k; R0805
R2, R33, R38: 1.2k; R0805
R3, R40: 50k; R0805
R7, R8: 4.7k; R0805
R10, R11: 4.2k; R0805
R12: 200k; R0805
R14, R17: 41.2k; R0805
R15, R23: 1M; R0805
R16: 88.7k; R0805
R18: 510; R0805
R21: 6.8k; R0805
R24: 243k; R0805
R25, R30, R35: 10; R0805
R31: 270; R0805
R32: 1.5k; R0805
R34: 68; R0805
THRUST1, THRUST2, THRUST3, THRUST4, THRUST5, THRUST6, THRUST7, THRUST8: KK254_VERT_4PIN22-29-2041; KK254_VERT_4PIN
THRUSTER_CURR_ADC: ADS7828; TSSOP16
TVS1, TVS2, TVS3: ESD12VD3B; SOD-323
U1: PCA9685; TSSOP-28_4MM
U$1, U$66: SSM3J353F; SOT-346-3/S-MINI
U$2, U$4, U$8, U$11, U$14, U$17, U$19, U$23, U$29, U$35, U$39: ACS713SOIC; ACS713-SOIC
U$3: TIVA-C_EVAL
U$5: 25A Fuse; 1.25"_FUSECLIPS
U$6, U$9, U$12, U$15, U$18, U$20, U$27, U$36, U$37, U$40: 4A Fuse; 154-OMNI-BLOK
U$7, U$10, U$13, U$16, U$22, U$26, U$28, U$30, U$31, U$32, U$33, U$34, U$38, U$59: VTVS; DO-219AB
U$45: 74LVC1G14; TSSOP5
V-THRUST_CURR_ADC: ADC121C021; VSSOP-8
V-THRUST_LED: 0805_LED; 0805
V-THRUST_OUT: Vin_OUT; KK254_VERT_2PIN
V-THRUST_VOLTAGE: INA219SOT23; SOT-23-8

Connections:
3V3: BME280.P$2 (!CS), BME280.P$5 (SDO/ADR), BME280.P$6 (VDDIO), BME280.P$8 (VDD), C24.1, C25.1, C26.1, C44.1, C83.1, C84.1, C85.1, I2C_SHIFT.P$2 (VREF1), R10.2, R11.2, R34.2, U$3.1-1 (3V3)
5V: 5-TVS_1.P$1, 5-TVS_1.P$3, 5-TVS_1.P$4, 5-TVS_1.P$6, 5-TVS_2.P$1, 5-TVS_2.P$3, 5-TVS_2.P$4, 5-TVS_2.P$6, 5V_CURR_ADC.P$5 (VDD), 5V_CURR_ADC.P$6 (ADR1), 5V_OUT.P$1, 5V_VOLTAGE.P$4 (VS), 12V_CURR_ADC.P$5 (VDD), 12V_VOLTAGE.P$4 (VS), 12V_VOLTAGE.P$8 (A1), C1.1, C5.1, C7.1, C8.1, C11.1, C14.1, C17.1, C19.1, C22.1, C33.1, C43.1, C48.1, C51.1, C53.1, C56.1, C67.1, C68.1, C81.1, C82.1, C93.1, C95.1, C96.1, C97.1, C98.1, C99.1, C100.1, DEPTH_SENS.P$4, ETHERNET.P$1, FAN1.P$1, FAN2.P$1, R1.2, R7.2, R8.2, R12.2, R21.2, R31.2, R35.1, THRUSTER_CURR_ADC.10 (REF), THRUSTER_CURR_ADC.16 (VDD), U1.1 (A0), U1.2 (A1), U1.3 (A2), U1.4 (A3), U1.5 (A4), U1.24 (A5), U1.28 (VDD), U$3.3-1 (5V), U$4.P$8 (VCC), U$8.P$8 (VCC), U$11.P$8 (VCC), U$14.P$8 (VCC), U$17.P$8 (VCC), U$19.P$8 (VCC), U$20.P$2, U$23.P$8 (VCC), U$29.P$8 (VCC), U$35.P$8 (VCC), U$39.P$8 (VCC), U$45.P$5 (VDD), V-THRUST_CURR_ADC.P$3 (ADR0), V-THRUST_CURR_ADC.P$5 (VDD), V-THRUST_CURR_ADC.P$6 (ADR1), V-THRUST_VOLTAGE.P$4 (VS), V-THRUST_VOLTAGE.P$7 (A0), V-THRUST_VOLTAGE.P$8 (A1)
+12V: 12V_OUT.P$1, C45.1, C50.1, C77.1, C78.1, CPU_PWR.P$3, CPU_PWR.P$4, R25.1, R33.2, TVS1.P$1, TVS2.P$1, TVS3.P$1, U$36.P$2
AIN0: U$3.3-9 (PE3)
AIN1: U$3.3-8 (PE2)
AIN2: U$3.3-7 (PE1)
AIN3: U$3.2-3 (PE0)
AIN4: U$3.3-6 (PD3)
AIN5: U$3.3-5 (PD2)
AIN8: U$3.1-6 (PE5)
AIN9: U$3.1-5 (PE4)
AIN10: U$3.1-7 (PB4)
AIN11: U$3.1-2 (PB5)
CPU_ON: 12V_REG.14 (EN/UV), JP1.2, U$45.P$4 (OUT)
GND: 3V3_LED.P$2 (C), 5-TVS_1.P$2, 5-TVS_1.P$5, 5-TVS_2.P$2, 5-TVS_2.P$5, 5V_CURR_ADC.P$3 (ADR0), 5V_CURR_ADC.P$7 (GND), 5V_LED.P$2 (C), 5V_OUT.P$2, 5V_PG.C, 5V_REG.6 (GND-1), 5V_REG.7 (GND-1), 5V_REG.10 (GND-2), 5V_REG.11 (GND-2), 5V_REG.18 (GND), 5V_VOLTAGE.P$3 (GND), 5V_VOLTAGE.P$7 (A0), 5V_VOLTAGE.P$8 (A1), 12V_CURR_ADC.P$3 (ADR0), 12V_CURR_ADC.P$6 (ADR1), 12V_CURR_ADC.P$7 (GND), 12V_LED.P$2 (C), 12V_OUT.P$2, 12V_REG.6 (GND-1), 12V_REG.7 (GND-1), 12V_REG.10 (GND-2), 12V_REG.11 (GND-2), 12V_REG.18 (GND), 12V_VOLTAGE.P$3 (GND), 12V_VOLTAGE.P$7 (A0), BME280.P$1 (GND1), BME280.P$7 (GND2), C1.2, C2.2, C3.2, C4.2, C5.2, C6.2, C7.2, C8.2, C9.2, C10.2, C11.2, C12.2, C13.2, C14.2, C15.2, C16.2, C17.2, C18.2, C19.2, C20.2, C21.2, C22.2, C23.2, C24.2, C25.2, C26.2, C27.2, C29.2, C30.2, C31.2, C32.2, C33.2, C34.2, C35.2, C36.P$2 (-), C37.2, C38.2, C39.2, C40.2, C43.2, C44.2, C45.2, C46.2, C47.2, C48.2, C49.2, C50.2, C51.2, C52.2, C53.2, C54.2, C55.2, C56.2, C57.2, C58.2, C60.2, C61.2, C62.P$2 (-), C63.2, C67.2, C68.2, C77.2, C78.2, C81.2, C82.2, C83.2, C84.2, C85.2, C86.2, C87.2, C88.2, C89.2, C90.2, C91.2, C92.2, C93.2, C95.2, C96.2, C97.2, C98.2, C99.2, C100.2, CAMERA1.P$2, CAMERA2.P$2, CPU_ON.P$2, CPU_PWR.P$1, CPU_PWR.P$2, DEPTH_SENS.P$3, ETHERNET.P$2, FAN1.P$2, FAN2.P$2, I2C_SHIFT.P$1 (GND), JP2.P$1, LED2.C, R14.1, R16.1, R17.1, R24.1, THRUST1.P$1, THRUST1.P$3, THRUST2.P$1, THRUST2.P$3, THRUST3.P$1, THRUST3.P$3, THRUST4.P$1, THRUST4.P$3, THRUST5.P$1, THRUST5.P$3, THRUST6.P$1, THRUST6.P$3, THRUST7.P$1, THRUST7.P$3, THRUST8.P$1, THRUST8.P$3, THRUSTER_CURR_ADC.9 (GND), THRUSTER_CURR_ADC.11 (COM), THRUSTER_CURR_ADC.12 (A0), THRUSTER_CURR_ADC.13 (A1), TVS1.P$2, TVS2.P$2, TVS3.P$2, U1.14 (VSS), U1.23 (!OE), U1.25 (EXTCLK), U$2.P$5 (GND), U$3.2-1 (GND), U$3.3-2 (GND), U$4.P$5 (GND), U$7.P$1 (A), U$8.P$5 (GND), U$10.P$1 (A), U$11.P$5 (GND), U$13.P$1 (A), U$14.P$5 (GND), U$16.P$1 (A), U$17.P$5 (GND), U$19.P$5 (GND), U$22.P$1 (A), U$23.P$5 (GND), U$26.P$1 (A), U$28.P$1 (A), U$29.P$5 (GND), U$30.P$1 (A), U$31.P$1 (A), U$32.P$1 (A), U$33.P$1 (A), U$34.P$1 (A), U$35.P$5 (GND), U$38.P$1 (A), U$39.P$5 (GND), U$45.P$3 (GND), U$59.P$1 (A), V-THRUST_CURR_ADC.P$7 (GND), V-THRUST_LED.P$2 (C), V-THRUST_OUT.P$2, V-THRUST_VOLTAGE.P$3 (GND)
unnamed: 12V_REG.15 (RT), R14.2
unnamed: R1.1, U$3.2-5 (!RESET!)
unnamed: 5V_PG.A, R2.1
unnamed: R2.2, U$1.P$2 (D)
unnamed: 5V_REG.19 (PG), R3.1, U$1.P$1 (G)
unnamed: 12V_REG.1 (BIAS), C28.1, C35.1, C36.P$1 (+), L2.P$2 (2), R15.2, U$35.P$1 (IP+), U$35.P$2 (IP+)
unnamed: 5V_REG.15 (RT), R17.2
unnamed: C3.1, U$2.P$6 (FILTER)
unnamed: C9.1, U$8.P$6 (FILTER)
unnamed: C6.1, U$4.P$6 (FILTER)
unnamed: C54.1, C86.1, THRUST1.P$4, U$6.P$2, U$31.P$2 (C)
unnamed: U$4.P$3 (IP-), U$4.P$4 (IP-), U$6.P$1
unnamed: C10.1, C88.1, THRUST2.P$4, U$9.P$2, U$30.P$2 (C)
unnamed: U$8.P$3 (IP-), U$8.P$4 (IP-), U$9.P$1
unnamed: C12.1, U$11.P$6 (FILTER)
unnamed: C13.1, C87.1, THRUST3.P$4, U$12.P$2, U$26.P$2 (C)
unnamed: U$11.P$3 (IP-), U$11.P$4 (IP-), U$12.P$1
unnamed: C15.1, U$14.P$6 (FILTER)
unnamed: C16.1, C89.1, THRUST4.P$4, U$15.P$2, U$28.P$2 (C)
unnamed: U$14.P$3 (IP-), U$14.P$4 (IP-), U$15.P$1
unnamed: C18.1, U$17.P$6 (FILTER)
unnamed: C21.1, C91.1, THRUST5.P$4, U$18.P$2, U$22.P$2 (C)
unnamed: U$17.P$3 (IP-), U$17.P$4 (IP-), U$18.P$1
unnamed: C29.1, U$23.P$6 (FILTER)
unnamed: C30.1, C90.1, THRUST6.P$4, U$13.P$2 (C), U$27.P$2
unnamed: U$23.P$3 (IP-), U$23.P$4 (IP-), U$27.P$1
unnamed: C37.1, U$29.P$6 (FILTER)
unnamed: 12V_REG.8 (SW), 12V_REG.9 (SW), 12V_REG.21 (SW), 12V_REG.22 (SW), C41.2, L2.P$1 (1)
unnamed: C20.1, U$19.P$6 (FILTER)
unnamed: U$5.P$1, U$5.P$2, U$19.P$3 (IP-), U$19.P$4 (IP-)
unnamed: C55.1, C92.1, THRUST7.P$4, U$16.P$2 (C), U$37.P$2
unnamed: U$29.P$3 (IP-), U$29.P$4 (IP-), U$37.P$1
unnamed: C57.1, U$39.P$6 (FILTER)
unnamed: C52.1, C58.1, THRUST8.P$4, U$10.P$2 (C), U$40.P$2
unnamed: 5V_REG.8 (SW), 5V_REG.9 (SW), 5V_REG.21 (SW), 5V_REG.22 (SW), C65.2, L1.P$1 (1)
unnamed: C23.1, I2C_SHIFT.P$7 (VREF2), I2C_SHIFT.P$8 (EN), R12.1
unnamed: 5V_REG.20 (FB), C42.2, R23.1, R24.2
unnamed: 5V_REG.3 (BST), C65.1
unnamed: 12V_REG.20 (FB), C28.2, R15.1, R16.2
unnamed: 12V_REG.3 (BST), C41.1
unnamed: U$39.P$3 (IP-), U$39.P$4 (IP-), U$40.P$1
unnamed: 5V_REG.2 (INTV-CC), C63.1
unnamed: 12V_VOLTAGE.P$1 (IN+), 12V_VOLTAGE.P$2 (IN-), R25.2
unnamed: C31.1, U$35.P$6 (FILTER)
unnamed: U$19.P$7 (VIOUT), V-THRUST_CURR_ADC.P$4 (VIN)
unnamed: 12V_REG.2 (INTV-CC), C39.1
unnamed: U$2.P$3 (IP-), U$2.P$4 (IP-), U$20.P$1
unnamed: U$35.P$3 (IP-), U$35.P$4 (IP-), U$36.P$1
unnamed: 5V_CURR_ADC.P$4 (VIN), U$2.P$7 (VIOUT)
unnamed: R30.2, V-THRUST_VOLTAGE.P$1 (IN+), V-THRUST_VOLTAGE.P$2 (IN-)
unnamed: C32.1, R18.2, U$45.P$2 (IN)
unnamed: 12V_CURR_ADC.P$4 (VIN), U$35.P$7 (VIOUT)
unnamed: CPU_ON.P$1, R18.1, R21.1, U$59.P$2 (C)
unnamed: 5V_LED.P$1 (A), R31.1
unnamed: R32.1, V-THRUST_LED.P$1 (A)
unnamed: 12V_LED.P$1 (A), R33.1
unnamed: 3V3_LED.P$1 (A), R34.1
unnamed: 5V_VOLTAGE.P$1 (IN+), 5V_VOLTAGE.P$2 (IN-), R35.2
unnamed: LED2.A, R38.1
unnamed: R38.2, U$66.P$2 (D)
unnamed: 12V_REG.19 (PG), R40.1, U$66.P$1 (G)
RELAY_OUT: 5V_REG.4 (VIN-1), 5V_REG.13 (VIN-2), 5V_REG.14 (EN/UV), 12V_REG.4 (VIN-1), 12V_REG.13 (VIN-2), C4.1, C27.1, C34.1, C38.1, C40.1, C60.1, JP1.1, JP2.P$2, R3.2, R40.2, U$1.P$3 (S), U$7.P$2 (C), U$19.P$1 (IP+), U$19.P$2 (IP+), U$66.P$3 (S)
RX: U$3.1-3 (PB0)
SCL1: 5V_CURR_ADC.P$1 (SCL), 5V_VOLTAGE.P$5 (SCL), 12V_CURR_ADC.P$1 (SCL), 12V_VOLTAGE.P$5 (SCL), I2C_SHIFT.P$6 (SCL2), R8.1, THRUSTER_CURR_ADC.14 (SCL), U1.26 (SCL), U$3.1-9 (PA6), V-THRUST_CURR_ADC.P$1 (SCL), V-THRUST_VOLTAGE.P$5 (SCL)
SCL3: U$3.2-7 (PD0)
SCL-3V3: BME280.P$4 (SCK/SCL), DEPTH_SENS.P$1, I2C_SHIFT.P$3 (SCL1), R11.1
SDA1: 5V_CURR_ADC.P$8 (SDA), 5V_VOLTAGE.P$6 (SDA), 12V_CURR_ADC.P$8 (SDA), 12V_VOLTAGE.P$6 (SDA), I2C_SHIFT.P$5 (SDA2), R7.1, THRUSTER_CURR_ADC.15 (SDA), U1.27 (SDA), U$3.1-10 (PA7), V-THRUST_CURR_ADC.P$8 (SDA), V-THRUST_VOLTAGE.P$6 (SDA)
SDA3: U$3.2-6 (PD1)
SDA-3V3: BME280.P$3 (SDI/SDA), DEPTH_SENS.P$2, I2C_SHIFT.P$4 (SDA1), R10.1
SW-5V: 5V_REG.1 (BIAS), C2.1, C42.1, C61.1, C62.P$1 (+), L1.P$2 (2), R23.2, U$2.P$1 (IP+), U$2.P$2 (IP+), U$2.P$8 (VCC)
T1_CURR: THRUSTER_CURR_ADC.1 (CH0), U$4.P$7 (VIOUT)
T1_PWM: THRUST1.P$2, U1.6 (CH0)
T2_CURR: THRUSTER_CURR_ADC.2 (CH1), U$8.P$7 (VIOUT)
T2_PWM: THRUST2.P$2, U1.7 (CH1)
T3_CURR: THRUSTER_CURR_ADC.3 (CH2), U$11.P$7 (VIOUT)
T3_PWM: THRUST3.P$2, U1.8 (CH2)
T4_CURR: THRUSTER_CURR_ADC.4 (CH3), U$14.P$7 (VIOUT)
T4_PWM: THRUST4.P$2, U1.9 (CH3)
T5_CURR: THRUSTER_CURR_ADC.5 (CH4), U$17.P$7 (VIOUT)
T5_PWM: THRUST5.P$2, U1.10 (CH4)
T6_CURR: THRUSTER_CURR_ADC.6 (CH5), U$23.P$7 (VIOUT)
T6_PWM: THRUST6.P$2, U1.11 (CH5)
T7_CURR: THRUSTER_CURR_ADC.7 (CH6), U$29.P$7 (VIOUT)
T7_PWM: THRUST7.P$2, U1.12 (CH6)
T8_CURR: THRUSTER_CURR_ADC.8 (CH7), U$39.P$7 (VIOUT)
T8_PWM: THRUST8.P$2, U1.13 (CH7)
TX: U$3.1-4 (PB1)
V_THRUST: C46.1, C47.1, C49.1, CAMERA1.P$1, CAMERA2.P$1, R30.1, R32.2, U$4.P$1 (IP+), U$4.P$2 (IP+), U$5.P$3, U$5.P$4, U$8.P$1 (IP+), U$8.P$2 (IP+), U$11.P$1 (IP+), U$11.P$2 (IP+), U$14.P$1 (IP+), U$14.P$2 (IP+), U$17.P$1 (IP+), U$17.P$2 (IP+), U$23.P$1 (IP+), U$23.P$2 (IP+), U$29.P$1 (IP+), U$29.P$2 (IP+), U$32.P$2 (C), U$33.P$2 (C), U$34.P$2 (C), U$38.P$2 (C), U$39.P$1 (IP+), U$39.P$2 (IP+), V-THRUST_OUT.P$1

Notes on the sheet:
Address: 1110111 (0x77)(BME)
Address: 1001000 (Thrust ADC)
Address: 1110111 (0x77) )(BAR30)
Address: 1010101 (12V ADC)
Address: 1011010 (VIN ADC)
Address: 1011001 (5V ADC)
PG is an open-drain fault pin.
Should these be 5V powered?

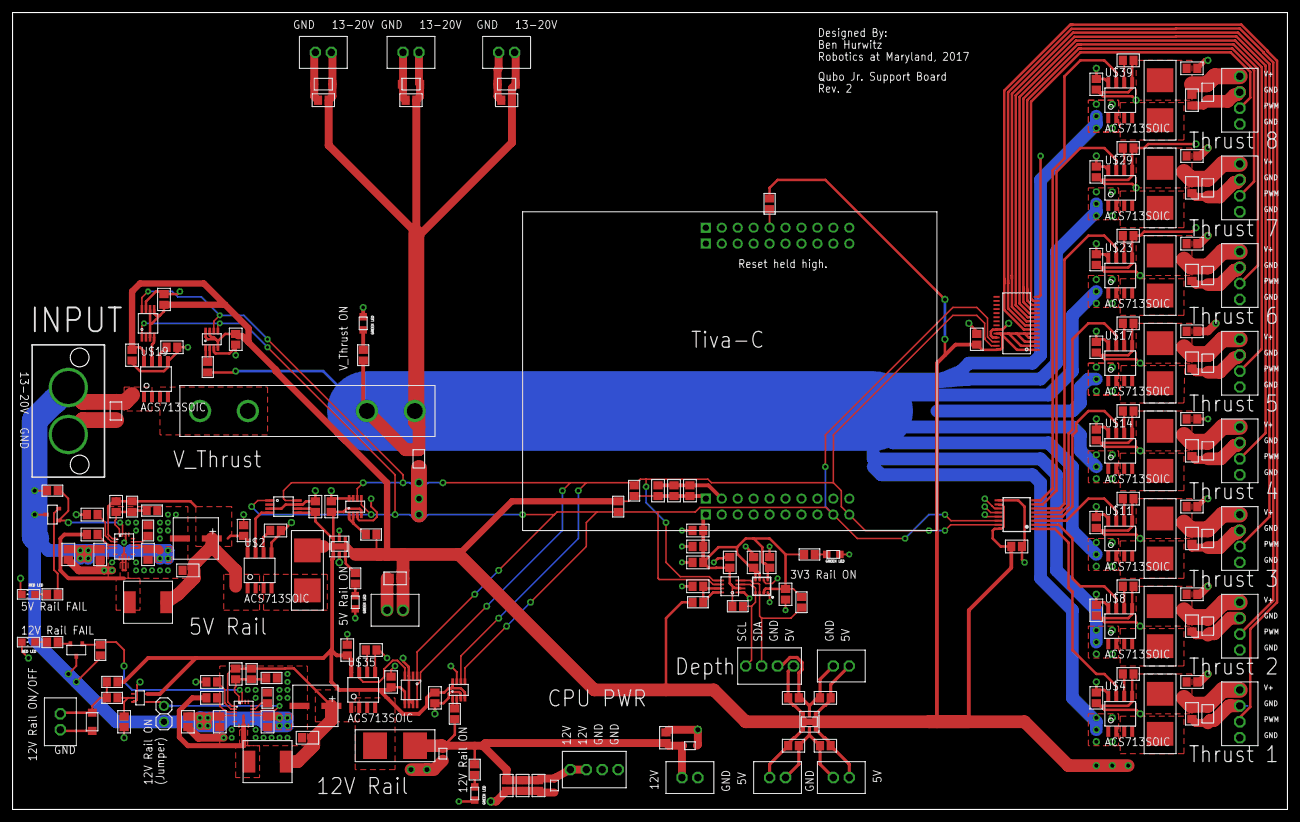
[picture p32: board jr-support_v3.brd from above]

Board: 2 copper layers, 203.2 x 127.0 mm, 197 parts (0 on the bottom side), 89 nets.

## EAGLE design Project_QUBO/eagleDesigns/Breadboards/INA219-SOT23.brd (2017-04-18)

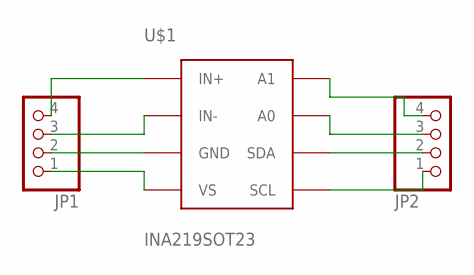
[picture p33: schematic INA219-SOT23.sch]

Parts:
JP1, JP2: PINHD-1X4; 1X04
U$1: INA219SOT23; SOT-23-8

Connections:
unnamed: JP1.4, U$1.P$1 (IN+)
unnamed: JP1.3, U$1.P$2 (IN-)
unnamed: JP1.2, U$1.P$3 (GND)
unnamed: JP1.1, U$1.P$4 (VS)
unnamed: JP2.1, U$1.P$5 (SCL)
unnamed: JP2.2, U$1.P$6 (SDA)
unnamed: JP2.3, U$1.P$7 (A0)
unnamed: JP2.4, U$1.P$8 (A1)


Board: 2 copper layers, 12.7 x 12.4 mm, 3 parts (0 on the bottom side), 8 nets.

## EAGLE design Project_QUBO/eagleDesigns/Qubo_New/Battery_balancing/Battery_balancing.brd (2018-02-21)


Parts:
C1: 150nF; C0805
C3: 6.8nF; C0805
C4: 22uF; C0805
JP1, JP2: 2_SUPERSABRE; SUPERSABRE_2CIRCUIT
LTC4364: LTC4364MSOP; MSOP16
M1, M2: IRF7458PBF; SOIC8
R1: 172K; R0805
R2: 10k; R0805
R3, R5: 10K; R0805
R4: 10; R0805
R6: 10m; 2827W
R7: 91K; R0805
R8: 5K; R0805

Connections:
BAT1: JP1.P$1, M1.D1 (D), M1.D2 (D), M1.D3 (D), M1.D4 (D), R1.2, R5.1
GND: C1.2, C3.2, C4.2, JP1.P$2, JP2.P$1, LTC4364.GND, R3.2, R8.2
unnamed: LTC4364.DGATE, M2.G1 (G)
unnamed: LTC4364.SOURCE, M1.S1 (S), M1.S2 (S), M1.S3 (S), M2.S1 (S), M2.S2 (S), M2.S3 (S)
unnamed: C1.1, LTC4364.TMR
unnamed: LTC4364.UV, R1.1, R2.1
unnamed: LTC4364.OV, R2.2, R3.1
unnamed: M1.G1 (G), R4.1
unnamed: LTC4364.FB, R7.2, R8.1
unnamed: C3.1, LTC4364.HGATE, R4.2
unnamed: LTC4364.SENSE, M2.D1 (D), M2.D2 (D), M2.D3 (D), M2.D4 (D), R6.P$1 (1)
unnamed: LTC4364.VCC, R5.2
unnamed: C4.1, JP2.P$2, LTC4364.OUT, R6.P$2 (2), R7.1


Board: 2 copper layers, 160.0 x 100.0 mm, 16 parts (0 on the bottom side), 13 nets.

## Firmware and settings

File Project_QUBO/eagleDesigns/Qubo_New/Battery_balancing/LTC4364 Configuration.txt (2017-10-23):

LTC4364 2017 CONFIGURATION:
	OV THRESHOLD: 1.25V(928.2+51K)/(51K) = 24V
	UV THRESHOLD: 1.25V(520.2K+51K)/(51K) = 14V
		OV/UV FILTERING CAPS tUV/tOV > 50
			OV CAP: ((1/51) + (1/931))^-1 * 0.1uF = 4.835 x 10 ^ -3 s 
			UV CAP: 4.835 / (50((1/51) + (1/523))^-1) = 2 nF
	FAULT TIMER

	

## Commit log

2016-09-08 initial commit: added Project QUBO folder
    [GPIO BOARD.brd, GPIO BOARD.sch, Power Supply Board.brd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]
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2016-10-02 edited power supply board sch
    [Power Supply Board.brd, Power Supply Board.sch]
2016-10-25 made new sch of power board to start anew
    [powerSupplyBoard_new.sch]
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2016-11-18 added diode OR/ hot swap to schematic
    [powerSupplyBoard_new.sch]
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2016-11-21 finished diode or/ hot swap on powerBoard/powerSupplyBoard_new.sch
    [powerSupplyBoard_new.sch]
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2016-11-23 update to motor control board
    linked current sensor to header, ADC, for one motor. added ultrafit
    (motor power) and supersabre (batery power) headers
    [MCB1.sch]
2016-11-30 update to MCB
    need to finalize pinouts on ADC and PWM controller, filer capacitors on
    current sensors, fuses
    [MCB1.sch]
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2017-01-27 finalize MCB
    Devices still need to have packages designed. Pneumatics board still
    needs to be integrated
    [MCB1.sch]
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2017-01-27 create motor control board board
    [MCB1.brd, MCB1.sch]
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2017-02-01 fixed psb brd errors
    [powerSupplyBoard_new.brd]
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2017-02-10 combined pneumatics and MCB
    [MCB1.sch]
2017-02-10 got rid of sense resistor on psb
    [powerSupplyBoard_new.brd, powerSupplyBoard_new.sch]
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2017-04-06 Charging board layout, rev. 1
    [DRILEGEND.CFG, charging_block.brd, charging_block.sch]
2017-04-06 finishing touches on oring board
    [ORing_block.brd, ORing_block.sch]
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2017-04-07 Added INA219 voltage sensors.
    [Mouser-order.xlsx, jr-support.sch]
2017-04-08 Charging board version 1 - completed
    [charging_block.brd, charging_block.sch]
2017-04-13 Main switch added to Jr Support.
    [jr-support.brd, jr-support.sch]
2017-04-18 Created breadboards. Added 5V reg PG fault line.
    [ACS713-SOIC8.brd, ACS713-SOIC8.sch, ADC121C021-VSSOP.brd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]
2017-04-18 Updated VS pin on INA219s to 5V
    [jr-support.brd, jr-support.sch]
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2017-08-08 Final update from Ben - updated documentation, electrical schematics and board layouts, and Eagle libraries.
    [07072017_request.xlsx, DRILEGEND.CFG, Mouser-order.xlsx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]
2017-10-02 Updated PTN78020 footprint (corrected Ales's incompetence)
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2017-10-13 Added the voltage divider's to the battery balancing board and updated the part's list
    [Powerboard Component List.xlsx]
2017-10-13 Reorganized the powerBoard folder
    [powerSupplyBoard_new.brd, powerSupplyBoard_new.sch]
2017-10-13 Added a .txt file showing all calculations for the board
    [LTC4364 Configuration.txt]
2017-10-17 Added supporting components for the SHDN pin to the schematic and part's list
    [Powerboard Component List.xlsx, powersupplyboardinprogress.sch]
2017-10-23 Changed some values for the OV and UV pins
    [LTC4364 Configuration.txt]
2017-10-27 Added a description of all the LTC4364 functionality (LTC4364 Notes.txt)
    [powersupplyboardinprogress.sch]
2017-11-07 Added the IRF7458PbF N-Channel MOSFET SMD Footprint to eagleLibraries
    [Powerboard Component List.xlsx, powersupplyboardinprogress.sch]
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2017-11-30 I created a new version of NewArmBoard
    [ArmBoardNew-New_Main_Board.brd, ArmBoardNew-New_Main_Board.sch, SIHMTEST.sch]
2017-12-07 formatted power board schematic layout
    [Powerboard.sch]
2018-01-20 updated armboard schematic and brd layout
    [ArmBoardNew-New_Main_Board.brd, ArmBoardNew-New_Main_Board.sch]
2018-01-22 created gerbers for arm board
    [ArmBoardNew-New_Main_Board.brd]
2018-01-25 Redesigned the battery balancing board
    [powersupplyboardinprogress.sch]
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2018-02-08 Battery Balancing Board Layout
    [testing_board.brd]
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2018-02-17 Revised the board layout
    [testing_board.brd]
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2018-02-21 Added Designed and Reviewed by messages to the silkscreen
    [testing_board.brd]
2018-02-28 Hypertonics board building
    I built a lot of the hypertonics board
    [Hypertronicsboard.sch]
2018-02-28 I added a maybe useful cam voltage source
    [Hypertronicsboard.sch]
2018-02-28 Nevermind, no camera voltage source
    [Hypertronicsboard.sch]
2018-02-28 Power board changes
    worked on layout and routing of power board
    [Powerboard.brd]
2018-03-02 PowerBoard update
    Updated powerboard wiring, and resized.
    [Powerboard.brd]
2018-03-09 Finished PowerboardRev1
    Revision 1 of the Powerboard
    [Powerboard.brd]
2018-03-09 I did a cam
    I did a cam on the hypertonics board
    [Hypertronicsboard.brd, Hypertronicsboard.sch]
2018-03-13 Powerboard parts
    Added a parts excel spreadsheet for powerboard
    [Robotics Powerboard Part List.xlsx]
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2018-03-18 Finished Powerboard Spreadsheet
    It is done
    [Robotics Powerboard Part List.xlsx]
2018-03-28 Capacitor and Powerboard
    Added capacitor package and adjusted powerboard
    [Powerboard.brd, Powerboard.sch]
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2018-09-26 this power board should be fixed
    I had to fix anthony's screwed up board
    [Powerboard.brd, Powerboard.sch]
2018-10-02 Fix to powerboard
    Minor errors corrected to power board
    [Powerboard.brd, Powerboard.sch]
2018-10-16 misc
    some small relabling of a board or two and I retrieved a fixed version of the formerly broken arm board
    [ArmBoardNew-New_Main_Board.brd, ArmBoardNew-New_Main_Board.sch, BatteryHullBoard.brd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]
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2019-02-15 Changed diamter of holes on terminals to 40 mm and added routes from sda and sclto LIL_PWR terminal
    [Hypertronicsboard.brd, Hypertronicsboard.sch]
2019-02-24 Prolly random fixes
    I don't remember but it's probaly pretty good
    [ArmBoardNew-New_Main_Board.brd, ArmBoardNew-New_Main_Board.sch, Hypertronicsboard.brd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]
2019-02-24 Fixes to TIVA board
    Some of the pins were named wrong so I fixed them
    [ArmBoardNew-New_Main_Board.brd, ArmBoardNew-New_Main_Board.sch]
2019-02-24 Resolved merge conflict by incorporating both suggestions.
    [Hypertronicsboard.brd]
2019-02-24 minor hypertonix edits
    I changed the names of some headers and made some curved traces not curved
    [Hypertronicsboard.brd, Hypertronicsboard.sch]
2019-02-24 Changes to Tiva board
    I had to rewire some things
    [ArmBoardNew-New_Main_Board.brd, ArmBoardNew-New_Main_Board.sch, Hypertronicsboard.brd]
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2020-07-31 made hyperarmboard
    made newboard thatcombindes the hypertonics and arm board
    [HyperArmBoard.brd, HyperArmBoardREV2.brd, HyperArmBoardREV2.sch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]
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2020-10-15 fixingsynchronicity issues
    [Powerboard.brd, Powerboard.sch, PowerboardRev4.brd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]

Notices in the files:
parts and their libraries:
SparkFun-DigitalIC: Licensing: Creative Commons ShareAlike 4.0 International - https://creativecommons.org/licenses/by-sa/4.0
